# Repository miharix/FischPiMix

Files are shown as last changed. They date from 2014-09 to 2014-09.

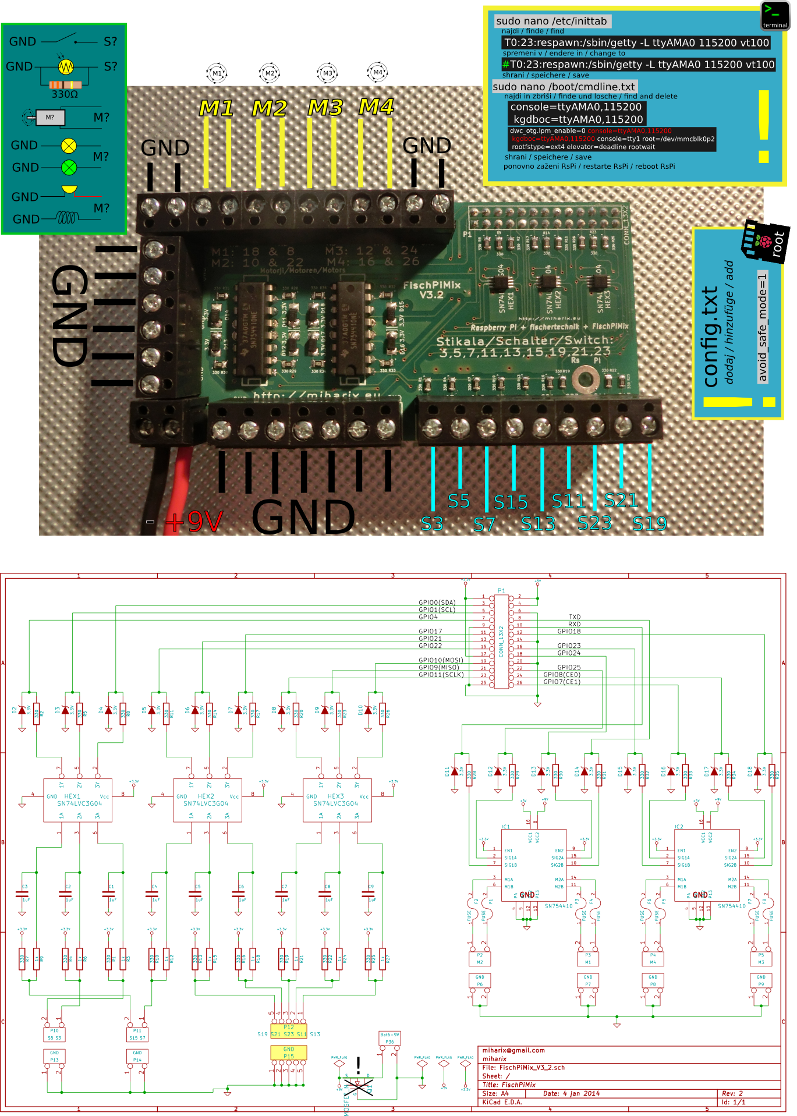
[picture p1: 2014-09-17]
FischPiMix_V3_2/porti.png

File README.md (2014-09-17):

https://www.youtube.com/watch?v=leHwTYAQO-k

https://www.youtube.com/watch?v=ODTY9RQhn2A

DE:
Den FishPiMix Modul habe ich entwickelt um in meiner Grundschule besser die Grundlagen der Robotik zu unterrichten. Momentan habe ich keine plane den FishPiMix zu produzieren, aber wen du meinst der FishPiMix ist etwas was du eventuell kaufen mochtest, schick mir eine PM und vielleicht ändere ich meine Meinung und produziere kleine Serie zum verkaufen.

Technische Daten:
* bis 4 Ft. Motoren in beide Richtungen oder bis 8 andere Verbraucher (Licht, El. Magnet,..) max 1A
* 9 Ein/Aus Schalter
+ Sicherungen gegen Überlastung
+ RsPi Ausgang Sicherung (wen man den Eingang als Ausgang betreibt)
+ Sicherung gegen falschen Batterie Polarität
+ Entprellung der Schalter 

ENG:
I made the FishPiMix module to better teach robotic in my primary class. At this moment I have no plans to making a FishPiMix for seling. But If you thing, FishPiMix is something you would like to buy, let me know. Maybe I'll change my mind and make a small quantity for selling. 

Technical data:
* max 4 Ft. motors individual controllable in both directions
* max 9 On/Off switches
+ fuses against overloading
+ RsPi GPIO protection against wrong direction (using an input as output)
+ Battery polarity protection
+ Button denounce circuit

SLO:
FishPiMix sem razvil za potrebe izbirnega predmeta v OŠ - Robotika v tehniki. Zaenkrat ne planiram prodajat module a če si učitelj(ca) in te zanima več o tem modulu mi piši, če vas bo več si mogoče premislim pa naredimo kako brezplačno delavnico. ;)

Tehnični podatki:
* 4 krtačnih motorčkov v obe smeri in z poljubno hitrostjo max 1A na motor
ali do 8 naprav npr žarnica, piskač... (vse iz FT kompletov) kjer lahko za vsako posebaj krmiliš napetost (PWM signal)
 * 9 on/off vhodov npr stikala, tipke, foto tranzistor (vse iz FT kompletov)
+ avtomatcke varovalke ob preobrementivi izhodov,
+ začito RPi če pomotoma nastaviš priključek on/off kot izhod in je stikalo sklenjeno (da ne skuriš RPi)
+ zaščito pred napačno prikločitvijo baterije za napajanje motorčkov (do 24V)
+ sistem za glajenje nečistih signalov zaradi uporabe slabih stikal (iskrenje)
+ vezje preprosto natakneš na RPi in dela

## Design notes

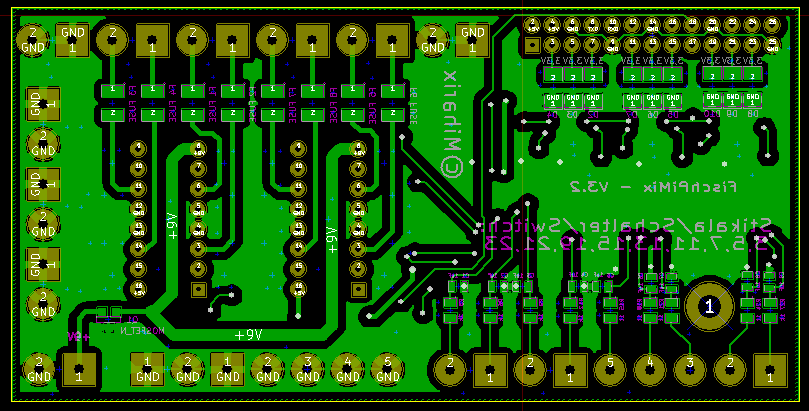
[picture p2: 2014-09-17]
FischPiMix_V3_2/pdf/FischPiMix_V3_2_B.png

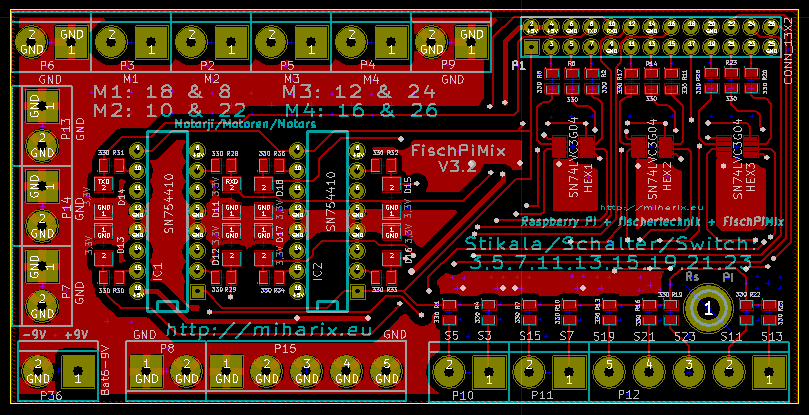
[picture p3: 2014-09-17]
FischPiMix_V3_2/pdf/FischPiMix_V3_2_F.png

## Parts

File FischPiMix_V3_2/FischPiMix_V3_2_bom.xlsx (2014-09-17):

min za 20 | cena ob 1 mix | 1 mix | sum | cena ob 50 mix | naročeno | url | podnožje
180 | 0.8 | 0.045 | 2.5 | 0.005 | 500 | http://si.farnell.com/multicomp/mcca000530/cap-ceramic-1uf-16v5v-0603/dp/1759408 | 603 | 1uF | 9 | C1 C2 C3 C4 C5 C6 C7 C8 C9
340 | 1.8 | 0.442 | 13 | 0.026 | 500 | http://si.farnell.com/on-semiconductor/mmsz3v3t1g/diode-zener-3-3v-0-5w/dp/1431266 | SOD-123/SM1206POL | 3,3V | 17 | D2 D3 D4 D5 D6 D7 D8 D9 D10 D11 D12 D13 D14 D15 D16 D17 D18
0 | 0.93 | 0 | 9.45 | 0.189 | 50 | http://si.farnell.com/international-rectifier/irlml6344trpbf/mosfet-n-ch-30v-5a-sot23/dp/1857299 | SOT-23 | IRLML6344TRPBF |  | Q1
160 | 2.432 | 0.896 | 16.8 | 0.112 | 150 | http://si.farnell.com/multicomp/mc33191/fuse-ptc-reset-smd-8v-500ma/dp/1800751RL | SM1210 | FUSE | 8 | F1 F2 F3 F4 F5 F6 F7 F8
40 | 5.72 | 3.92 | 39.2 | 1.96 | 20 | http://si.farnell.com/texas-instruments/sn754410neg4/ic-quadruple-half-h-driver-754410/dp/9592997 | DIP | SN754410 | 2 | IC1 IC2
520 | 5 | 0.026 | 5 | 0.001 | 5000 | http://si.farnell.com/multicomp/mc01w08051330r/resistor-330r-0-1w-1-0805-reel/dp/2129074 | 805 | 330 | 26 | R1 R2 R4 R5 R7 R8 R10 R11 R13 R14 R16 R17 R19 R20 R22 R23 R25 R26 R28 R29 R30 R31 R32 R33 R34 R35
180 | 5 | 0.009 | 5 | 0.001 | 5000 | http://si.farnell.com/multicomp/mc01w080511k/resistor-1k-0-1w-1-0805-reel/dp/2129113 | 805 | 1k | 9 | R3 R6 R9 R12 R15 R18 R21 R24 R27
60 | 0.39 | 0.93 | 12.4 | 0.31 | 40 | http://si.farnell.com/texas-instruments/sn74lvc3g04dctr/logic-inverter-gate-ssop-8/dp/2334920 | SSOP-8 | SN74LVC3G04DCTR | 3 | HEX1, HEX2, HEX3
0 |  | 0 | 6.24 | 0.156 | 40 | http://si.farnell.com/nxp/74hc04bq/ic-6-input-hex-inverter-dhvqfn14/dp/2164744 | SOT402-1 | DHVQFN14
20 |  | 0.35 | 35 | 0.35 | 100 | http://www.ebay.com/itm/100pcs-Pitch-2-54mm-2x40-Pin-Female-Double-Row-Pin-Straight-Header-Strip-/300740858603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 | DIP | CONN_13X2 | 1 | P1
40 | 5.1 | 1.02 | 10.2 | 0.51 | 20 | http://si.farnell.com/camdenboss/ctb1202-5bk/terminalblock-pcb-5way-5mm/dp/1716996 | DIP | CONNECTOR =5 pol | 2
160 | 2.496 | 1.072 | 10.72 | 0.134 | 80 | http://si.farnell.com/camdenboss/ctb1202-2bk/terminal-block-pcb-2way-16awg/dp/1716993 | DIP | Motor+bat9V+conn = 2pol | 8 | 4+1+2
1 | 27.67 |  | 27.67 |  | 1 |  |  | PI
 |  | 6.776666667 | 20.33 |  | 3 |  |  | pcb
 | 57.338 | 15.48666667 | 213.51
 | 28.868
 |  | en
 |  |  |  |  |  | http://si.farnell.com/multicomp/ss54/diode-schottk-rectif-5a-40v-smc/dp/1861427
 | http://www.elecrow.com/services-c-73/pcb-fabricate-service-c-73_116/2-layer-10cm-10cm-max-pcb-510pcs-color-free-p-328.html
1 | http://si.farnell.com/multicomp/jr1819-rohs-psg01769/socket-low-voltage-2-1mm-chassis/dp/1216726
1 | http://si.farnell.com/cliff-electronic-components/dcpp1/plug-dc-power-2-1mm-5a-pk10/dp/224923

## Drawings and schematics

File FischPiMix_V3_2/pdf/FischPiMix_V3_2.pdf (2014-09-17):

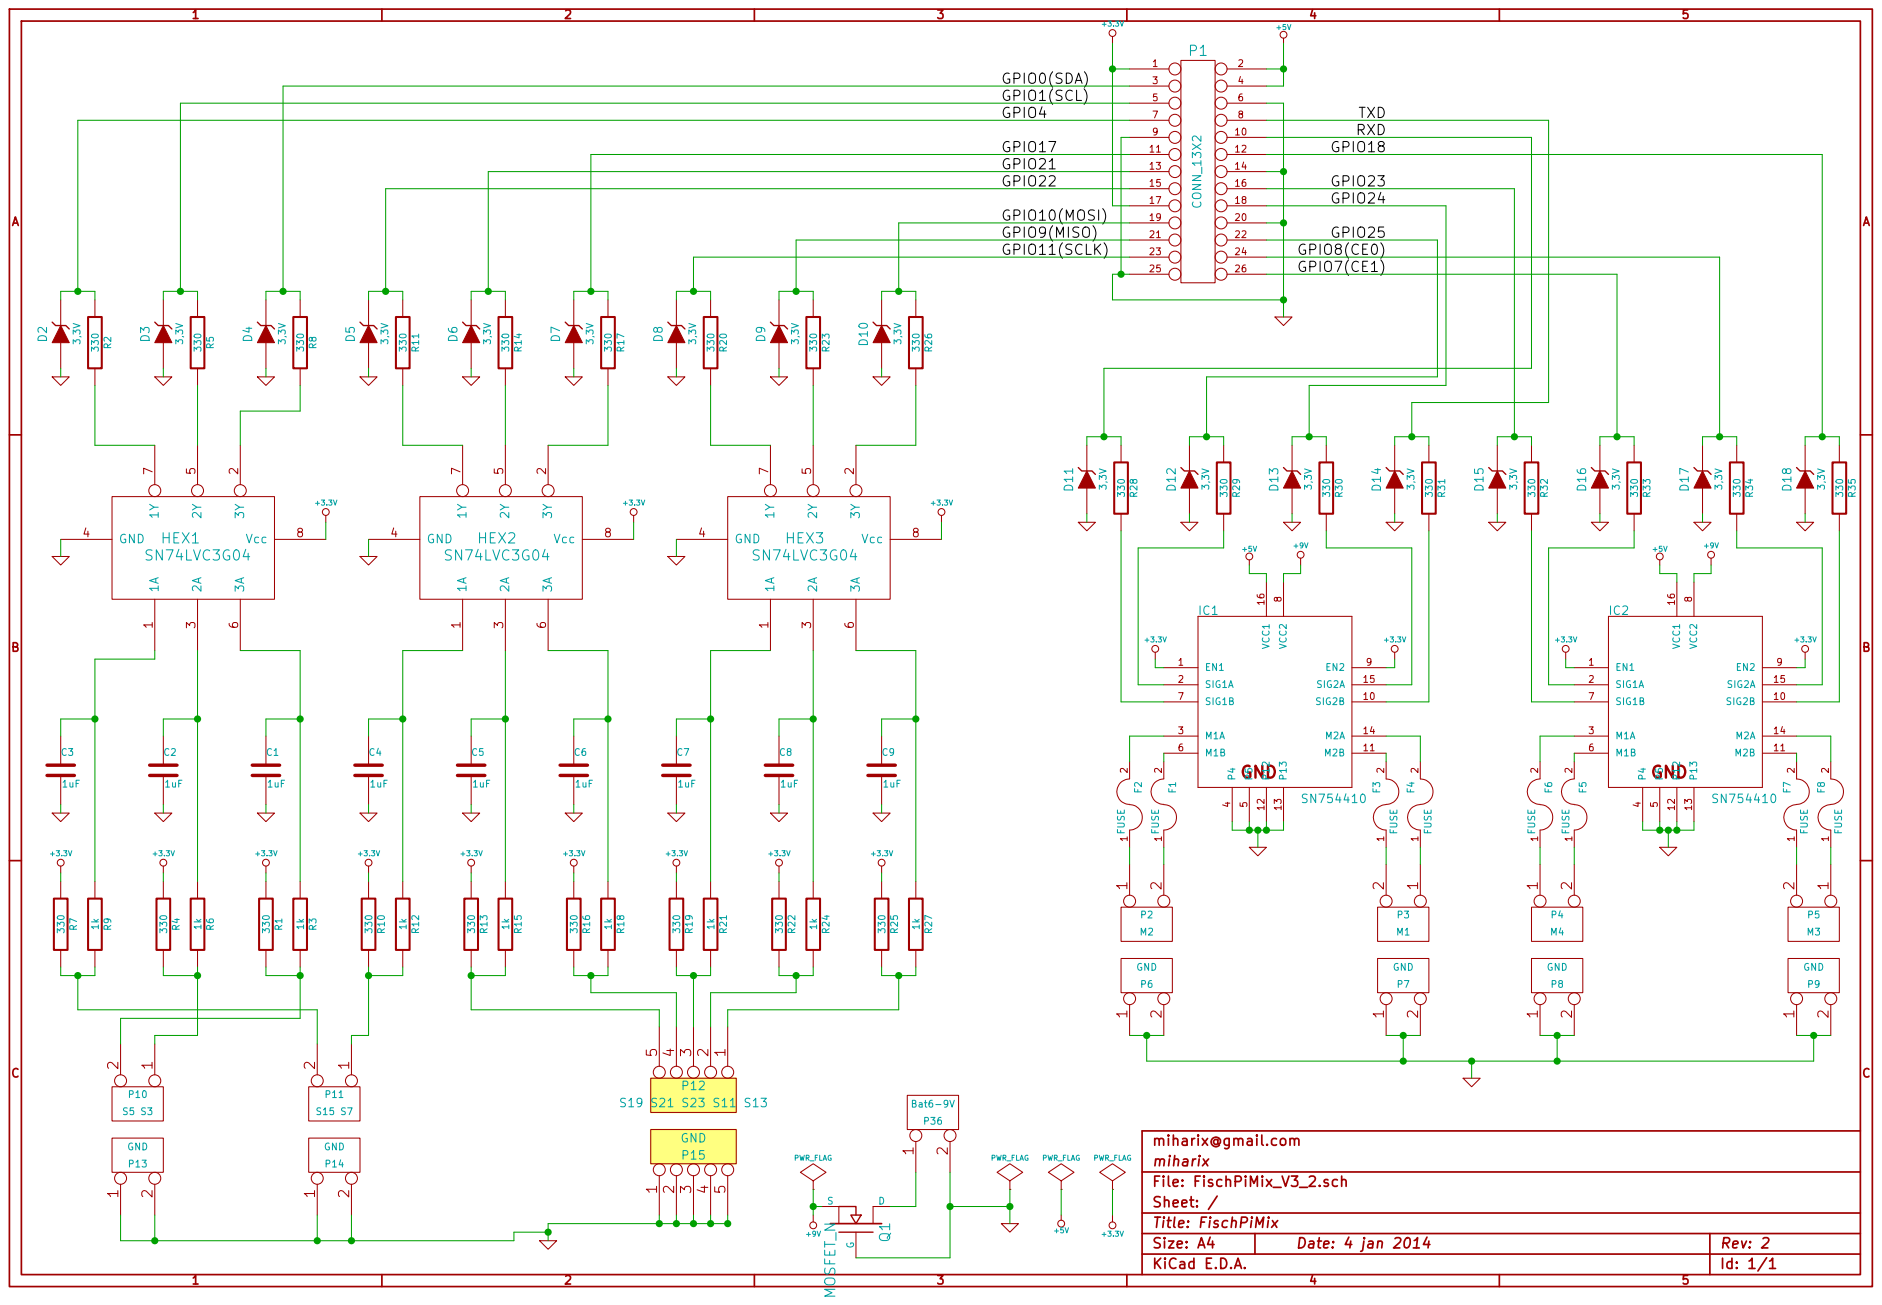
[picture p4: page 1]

GPIO1(SCL)

GPIO21 | | 13 | | 14 | GPIO23
GPIO22 | | 15 | | 16

17 | | 18 | GPIO24

21 | | 22
23 | | 24 | GPIO8(CE0)
25 | | 26 | GPIO7(CE1)

Sheet: / miharix miharix@gmail.com

Id: 1/1 Title: FischPiMix File: FischPiMix_V3_2.sch

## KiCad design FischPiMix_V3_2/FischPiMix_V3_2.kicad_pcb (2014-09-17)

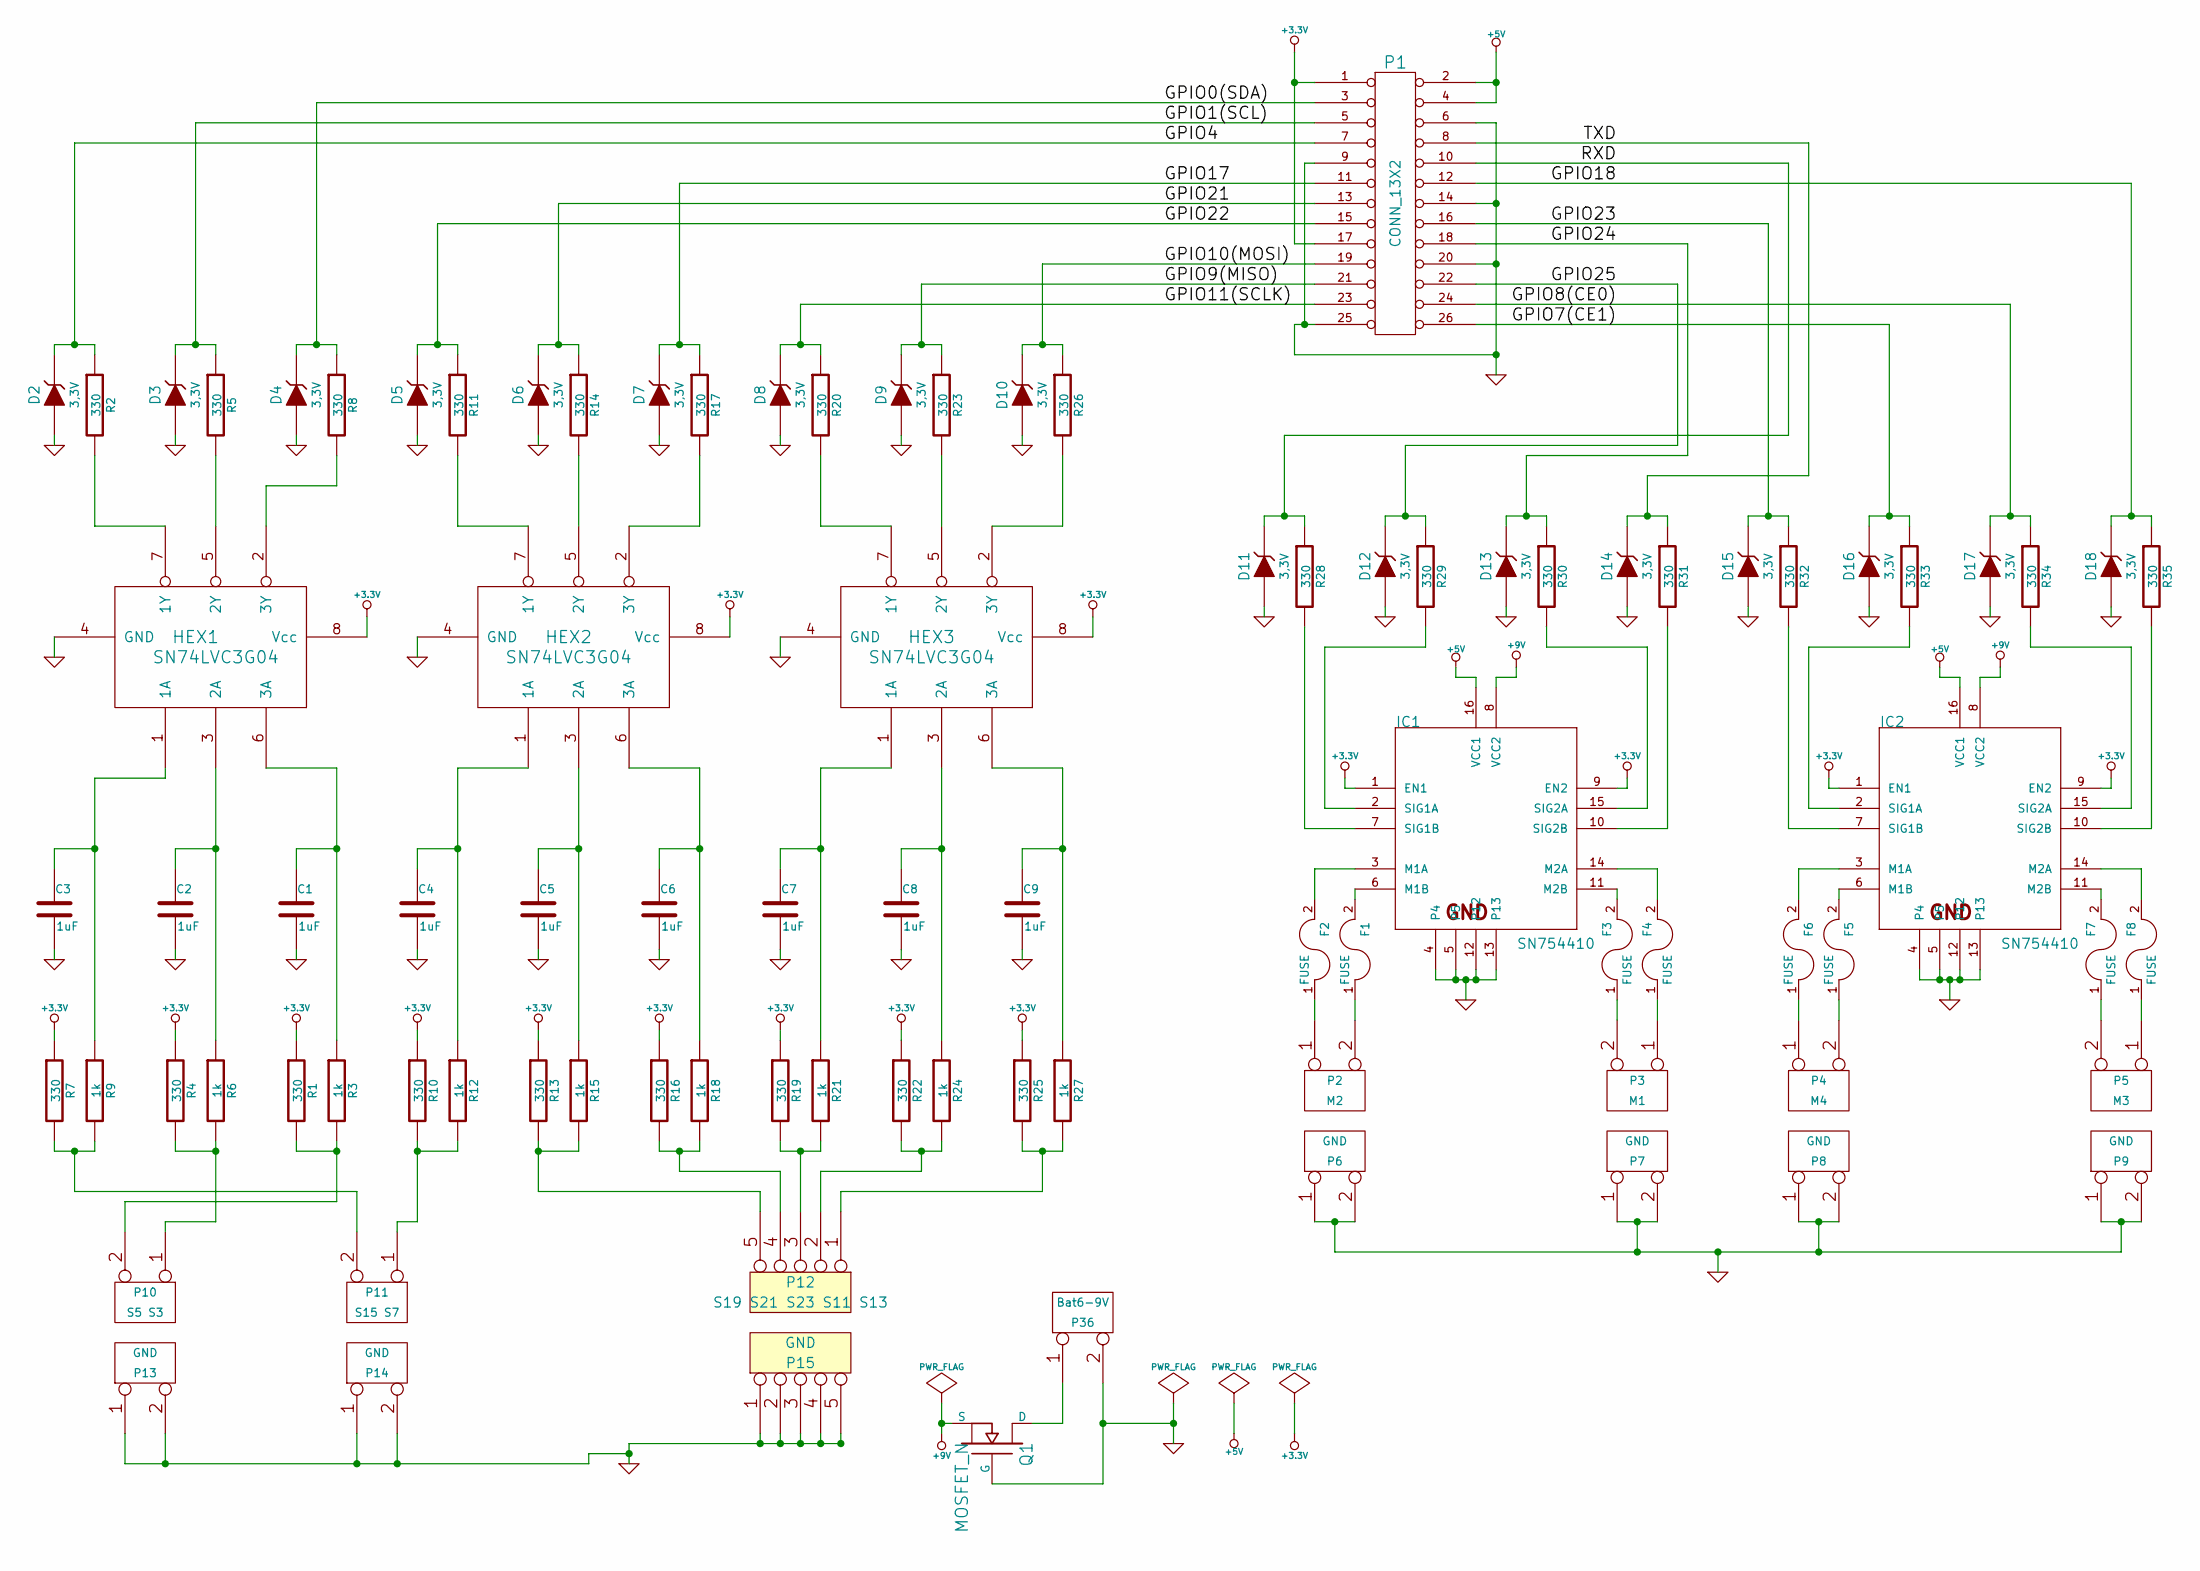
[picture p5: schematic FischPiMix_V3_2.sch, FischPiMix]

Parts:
C1, C2, C3, C4, C5, C6, C7, C8, C9: 1uF
D2, D3, D4, D5, D6, D7, D8, D9, D10, D11, D12, D13, D14, D15, D16, D17, D18: 3,3V
F1, F2, F3, F4, F5, F6, F7, F8: FUSE
HEX1, HEX2, HEX3: SN74LVC3G04
IC1, IC2: SN754410; HBridge-DIP16
P1: CONN_13X2
P2: M2
P3: M1
P4: M4
P5: M3
P6, P7, P8, P9, P13, P14, P15: GND
P10: S5 S3
P11: S15 S7
P12: S19 S21 S23 S11 S13
P36: Bat6-9V
Q1: MOSFET_N
R1, R2, R4, R5, R7, R8, R10, R11, R13, R14, R16, R17, R19, R20, R22, R23, R25, R26, R28, R29, R30, R31, R32, R33, R34, R35: 330
R3, R6, R9, R12, R15, R18, R21, R24, R27: 1k

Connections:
+3.3V: HEX1.8 (Vcc), HEX2.8 (Vcc), HEX3.8 (Vcc), IC1.1 (EN1), IC1.9 (EN2), IC2.1 (EN1), IC2.9 (EN2), P1.1, P1.17, R1.1, R4.1, R7.1, R10.1, R13.1, R16.1, R19.1, R22.1, R25.1
+5V: IC1.16 (VCC1), IC2.16 (VCC1), P1.2, P1.4
+9V: IC1.8 (VCC2), IC2.8 (VCC2), Q1.S
/GPIO0(SDA): D4.2 (K), P1.3, R8.1
/GPIO1(SCL): D3.2 (K), P1.5, R5.1
/GPIO4: D2.2 (K), P1.7, R2.1
/GPIO7(CE1): D16.2 (K), P1.26 (P22), R33.1
/GPIO8(CE0): D17.2 (K), P1.24 (P20), R34.1
/GPIO9(MISO): D9.2 (K), P1.21, R23.1
/GPIO10(MOSI): D10.2 (K), P1.19, R26.1
/GPIO11(SCLK): D8.2 (K), P1.23, R20.1
/GPIO17: D7.2 (K), P1.11, R17.1
/GPIO18: D18.2 (K), P1.12, R35.1
/GPIO21: D6.2 (K), P1.13, R14.1
/GPIO22: D5.2 (K), P1.15, R11.1
/GPIO23: D15.2 (K), P1.16, R32.1
/GPIO24: D13.2 (K), P1.18, R30.1
/GPIO25: D12.2 (K), P1.22, R29.1
/RXD: D11.2 (K), P1.10, R28.1
/TXD: D14.2 (K), P1.8, R31.1
GND: C1.2, C2.2, C3.2, C4.2, C5.2, C6.2, C7.2, C8.2, C9.2, D2.1 (A), D3.1 (A), D4.1 (A), D5.1 (A), D6.1 (A), D7.1 (A), D8.1 (A), D9.1 (A), D10.1 (A), D11.1 (A), D12.1 (A), D13.1 (A), D14.1 (A), D15.1 (A), D16.1 (A), D17.1 (A), D18.1 (A), HEX1.4 (GND), HEX2.4 (GND), HEX3.4 (GND), IC1.4, IC1.5, IC1.12, IC1.13, IC2.4, IC2.5, IC2.12, IC2.13, P1.6, P1.9, P1.14, P1.20, P1.25 (P24), P6.1, P6.2 (PM), P7.1, P7.2 (PM), P8.1, P8.2 (PM), P9.1, P9.2 (PM), P13.1, P13.2 (PM), P14.1, P14.2 (PM), P15.1, P15.2, P15.3, P15.4, P15.5, P36.2 (PM), Q1.G
unnamed: IC1.7 (SIG1B), R28.2
unnamed: IC1.10 (SIG2B), R31.2
unnamed: C6.1, HEX2.6 (3A), R18.1
unnamed: C7.1, HEX3.1 (1A), R21.1
unnamed: HEX2.2 (3Y), R17.2
unnamed: HEX2.5 (2Y), R14.2
unnamed: P12.5, R13.2, R15.2
unnamed: C8.1, HEX3.3 (2A), R24.1
unnamed: C9.1, HEX3.6 (3A), R27.1
unnamed: F6.2, IC2.3 (M1A)
unnamed: F7.1, P5.2 (PM)
unnamed: F3.1, P3.2 (PM)
unnamed: F4.1, P3.1
unnamed: F2.1, P2.1
unnamed: F1.1, P2.2 (PM)
unnamed: F8.2, IC2.14 (M2A)
unnamed: F7.2, IC2.11 (M2B)
unnamed: F8.1, P5.1
unnamed: F5.2, IC2.6 (M1B)
unnamed: IC2.10 (SIG2B), R35.2
unnamed: IC2.15 (SIG2A), R34.2
unnamed: IC2.7 (SIG1B), R32.2
unnamed: IC2.2 (SIG1A), R33.2
unnamed: IC1.15 (SIG2A), R30.2
unnamed: IC1.2 (SIG1A), R29.2
unnamed: F4.2, IC1.14 (M2A)
unnamed: F3.2, IC1.11 (M2B)
unnamed: F2.2, IC1.3 (M1A)
unnamed: F1.2, IC1.6 (M1B)
unnamed: F5.1, P4.2 (PM)
unnamed: F6.1, P4.1
unnamed: HEX1.2 (3Y), R8.2
unnamed: P11.2 (PM), R7.2, R9.2
unnamed: P10.2 (PM), R1.2, R3.2
unnamed: HEX3.5 (2Y), R23.2
unnamed: HEX3.7 (1Y), R20.2
unnamed: HEX3.2 (3Y), R26.2
unnamed: HEX2.7 (1Y), R11.2
unnamed: HEX1.5 (2Y), R5.2
unnamed: HEX1.7 (1Y), R2.2
unnamed: C1.1, HEX1.6 (3A), R3.1
unnamed: C2.1, HEX1.3 (2A), R6.1
unnamed: C5.1, HEX2.3 (2A), R15.1
unnamed: C3.1, HEX1.1 (1A), R9.1
unnamed: C4.1, HEX2.1 (1A), R12.1
unnamed: P12.3, R19.2, R21.2
unnamed: P12.4, R16.2, R18.2
unnamed: P12.2, R22.2, R24.2
unnamed: P12.1, R25.2, R27.2
unnamed: P10.1, R4.2, R6.2
unnamed: P11.1, R10.2, R12.2
unnamed: P36.1, Q1.D

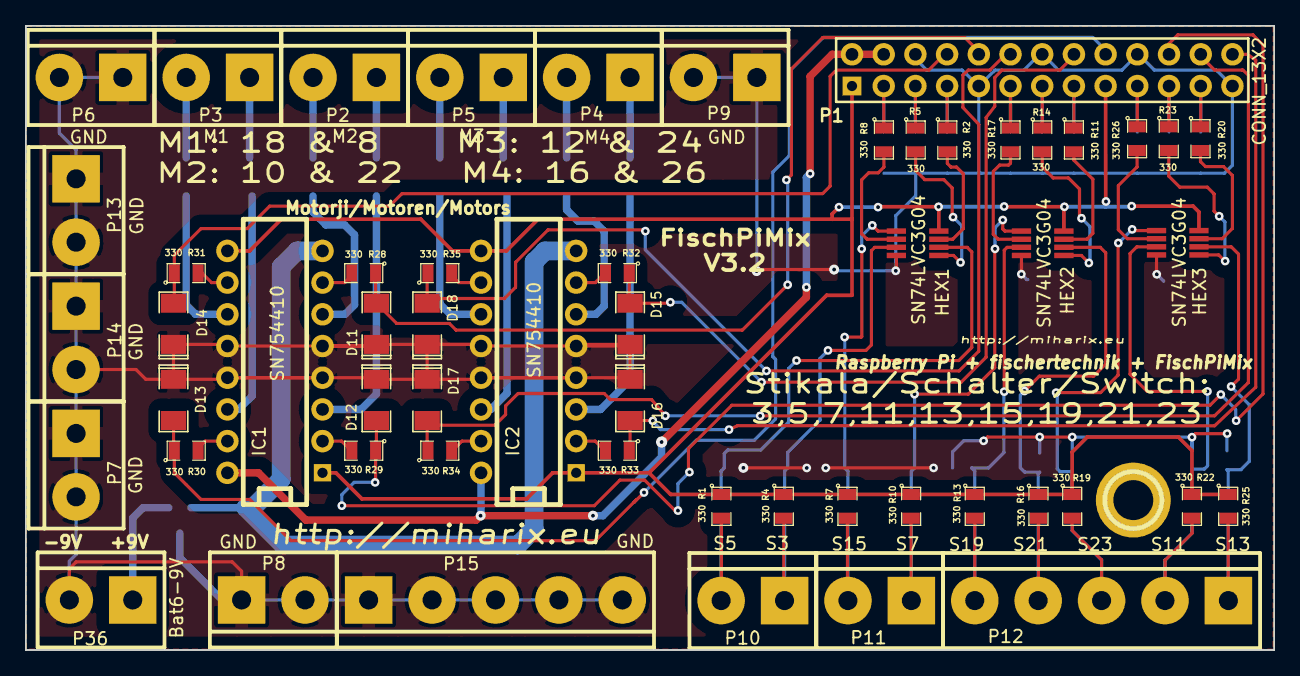
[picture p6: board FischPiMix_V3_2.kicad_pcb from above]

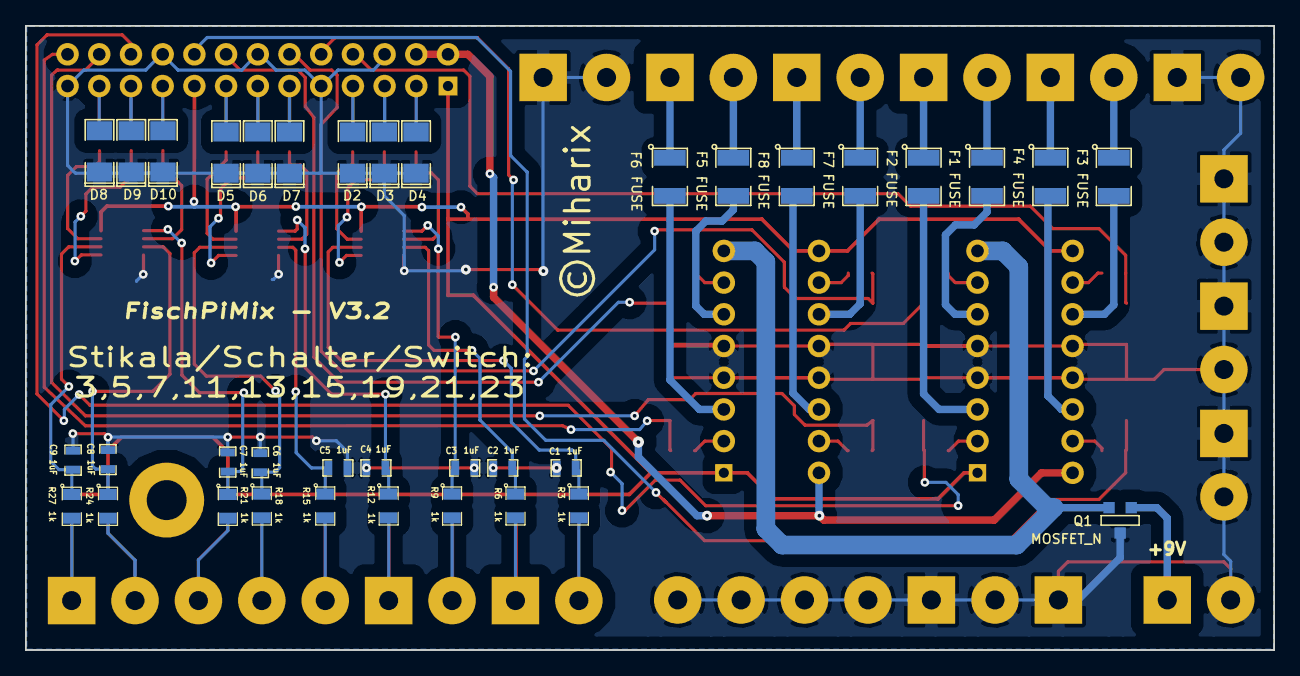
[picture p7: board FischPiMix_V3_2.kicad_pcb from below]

Board: 2 copper layers, 100.0 x 50.0 mm, 92 parts (36 on the bottom side), 73 nets.

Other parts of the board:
Rs: PI; 1pin

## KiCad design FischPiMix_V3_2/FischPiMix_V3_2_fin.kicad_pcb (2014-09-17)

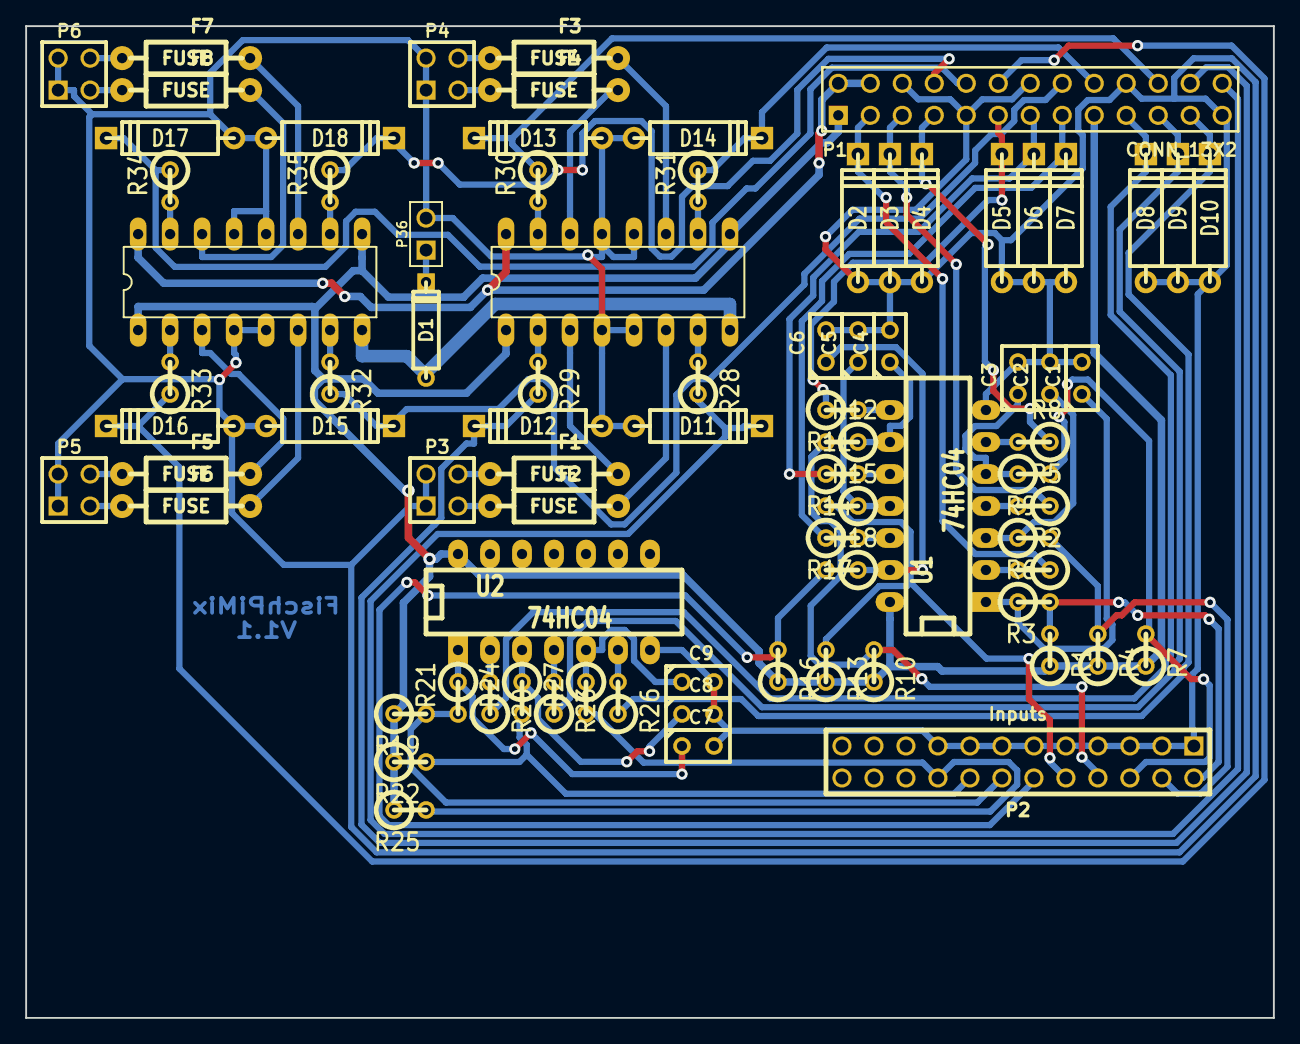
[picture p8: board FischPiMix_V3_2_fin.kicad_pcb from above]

Board: 2 copper layers, 99.1 x 78.7 mm, 81 parts (0 on the bottom side), 73 nets.

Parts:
C1, C2, C3, C4, C5, C6, C7, C8, C9: 1uF; C1
D1: DIODE; D3
D2, D3, D4, D5, D6, D7, D8, D9, D10, D11, D12, D13, D14, D15, D16, D17, D18: 3,3V; D4
F1, F2, F3, F4, F5, F6, F7, F8: FUSE; R250-4
IC1, IC2: SN754410; HBridge-DIP16
P1: CONN_13X2; pin_array_13x2
P2: Inputs; pin_array_12x2
P3: Motor1; PIN_ARRAY_2X2
P4: Motor2; PIN_ARRAY_2X2
P5: Motor3; PIN_ARRAY_2X2
P6: Motor4; PIN_ARRAY_2X2
P36: Bat9V; PIN_ARRAY_2X1
R1, R2, R4, R5, R7, R8, R10, R11, R13, R14, R16, R17, R19, R20, R22, R23, R25, R26, R28, R29, R30, R31, R32, R33, R34, R35: 330; R1
R3, R6, R9, R12, R15, R18, R21, R24, R27: 1k; R1
U1, U2: 74HC04; DIP-14__300_ELL

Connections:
+3.3V: IC1.1, IC1.9, IC2.1, IC2.9, P1.1, P1.17, R1.1, R4.1, R7.1, R10.1, R13.1, R16.1, R19.1, R22.1, R25.1, U1.14, U2.14
+5V: IC1.16, IC2.16, P1.2, P1.4
+9V: D1.1, IC1.8, IC2.8
/GPIO0(SDA): D2.2, P1.3, R2.1
/GPIO1(SCL): D3.2, P1.5, R5.1
/GPIO4: D4.2, P1.7, R8.1
/GPIO9(MISO): D9.2, P1.21, R23.1
/GPIO10(MOSI): D8.2, P1.19, R20.1
/GPIO11(SCLK): D10.2, P1.23, R26.1
/GPIO17: D5.2, P1.11, R11.1
/GPIO18: D16.2, P1.12, R33.1
/GPIO21: D6.2, P1.13, R14.1
/GPIO22: D7.2, P1.15, R17.1
/GPIO23: D15.2, P1.16, R32.1
/GPIO24: D14.2, P1.18, R31.1
/GPIO25: D13.2, P1.22, R30.1
/RXD: D17.2, P1.10, R34.1
/TXD: D18.2, P1.8, R35.1
GND: C1.2, C2.2, C3.2, C4.2, C5.2, C6.2, C7.2, C8.2, C9.2, D2.1, D3.1, D4.1, D5.1, D6.1, D7.1, D8.1, D9.1, D10.1, D11.1, D12.1, D13.1, D14.1, D15.1, D16.1, D17.1, D18.1, IC1.4, IC1.5, IC1.12, IC1.13, IC2.4, IC2.5, IC2.12, IC2.13, P1.6, P1.9, P1.14, P1.20, P1.25, P2.1, P2.3, P2.5, P2.7, P2.9, P2.11, P2.13, P2.15, P2.17, P3.1, P3.2, P4.1, P4.2, P5.1, P5.2, P6.1, P6.2, P36.2, U1.7, U2.7
unnamed: P2.8, R10.2, R12.2
unnamed: R11.2, U1.8
unnamed: C5.1, R15.1, U1.11
unnamed: P2.10, R13.2, R15.2
unnamed: R14.2, U1.10
unnamed: C3.1, R9.1, U1.5
unnamed: P2.6, R7.2, R9.2
unnamed: R8.2, U1.6
unnamed: C4.1, R12.1, U1.9
unnamed: P2.14, R19.2, R21.2
unnamed: R20.2, U2.2
unnamed: C8.1, R24.1, U2.3
unnamed: P2.16, R22.2, R24.2
unnamed: R23.2, U2.4
unnamed: C6.1, R18.1, U1.13
unnamed: P2.12, R16.2, R18.2
unnamed: R17.2, U1.12
unnamed: C7.1, R21.1, U2.1
unnamed: F6.1, P5.3
unnamed: F5.1, P5.4
unnamed: C2.1, R6.1, U1.3
unnamed: P2.2, R1.2, R3.2
unnamed: R2.2, U1.2
unnamed: P2.4, R4.2, R6.2
unnamed: R5.2, U1.4
unnamed: D1.2, P36.1
unnamed: C1.1, R3.1, U1.1
unnamed: IC2.10, R35.2
unnamed: IC2.2, R33.2
unnamed: IC2.7, R32.2
unnamed: IC2.15, R34.2
unnamed: F6.2, IC2.6
unnamed: F5.2, IC2.3
unnamed: F7.2, IC2.11
unnamed: F8.2, IC2.14
unnamed: F1.1, P3.4
unnamed: IC1.2, R29.2
unnamed: IC1.7, R28.2
unnamed: IC1.15, R30.2
unnamed: IC1.10, R31.2
unnamed: F2.2, IC1.6
unnamed: F1.2, IC1.3
unnamed: F3.2, IC1.11
unnamed: F4.2, IC1.14
unnamed: F2.1, P3.3
unnamed: F3.1, P4.4
unnamed: F4.1, P4.3
unnamed: F7.1, P6.4
unnamed: F8.1, P6.3
unnamed: P2.18, R25.2, R27.2
unnamed: C9.1, R27.1, U2.5
unnamed: R26.2, U2.6
unnamed: D12.2, P1.24, R29.1
unnamed: D11.2, P1.26, R28.1

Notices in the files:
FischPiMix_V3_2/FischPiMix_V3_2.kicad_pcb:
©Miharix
